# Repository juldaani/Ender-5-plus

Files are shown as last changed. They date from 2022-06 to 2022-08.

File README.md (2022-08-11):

# Ender-5-plus
Installation instructions for Ender 5 Plus (original hardware):
- BIGTREETECH BTT OCTOPUS V1.1 32BIT 
- TMC2209 stepper drivers
- Raspberry Pi 4 Model B 8GB
- OctoPi 0.18.0
- OctoPrint 1.8.1
- Klipper

### Shortcuts
[Board wirings](https://github.com/juldaani/Ender-5-plus#board-wirings)

[Installation and configuration of OctoPi+OctoPrint+Klipper](https://github.com/juldaani/Ender-5-plus#install-octopioctoprintklipper-on-raspberry-pioctopus)

[Physical installation of Octopus board and Raspberry Pi + 3D-models for mounts](https://github.com/juldaani/Ender-5-plus#physical-installation-of-octopus-board-and-raspberry-pi)

### Links
Bigtreetech octopus github:
(https://github.com/bigtreetech/BIGTREETECH-OCTOPUS-V1.0)

Random Octopus installation guide:
https://www.makenprint.uk/3d-printing/3d-printing-guides/3d-printer-mainboard-installation-guides/btt-octopus-guides/btt-octopus-setup-guide/

# Board wirings

## 1. Remove all jumpers from the board
If there are any jumpers attached remove them before proceeding.

## 2. Set jumpers to UART mode for stepper motor drivers
mtp://HMD_Global_Nokia_8_NB1GAD1780406664/Internal%20shared%20storage/DCIM/Camera/IMG_20220811_184935.jpg
mtp://HMD_Global_Nokia_8_NB1GAD1780406664/Internal%20shared%20storage/DCIM/Camera/IMG_20220811_184957.jpg

## 3. Wiring between PSU and board
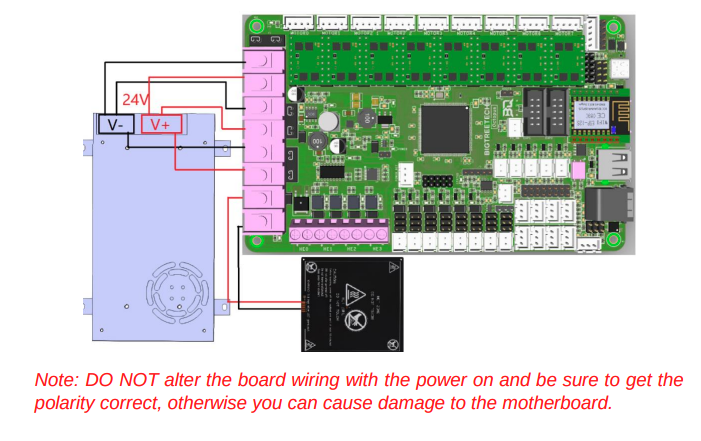
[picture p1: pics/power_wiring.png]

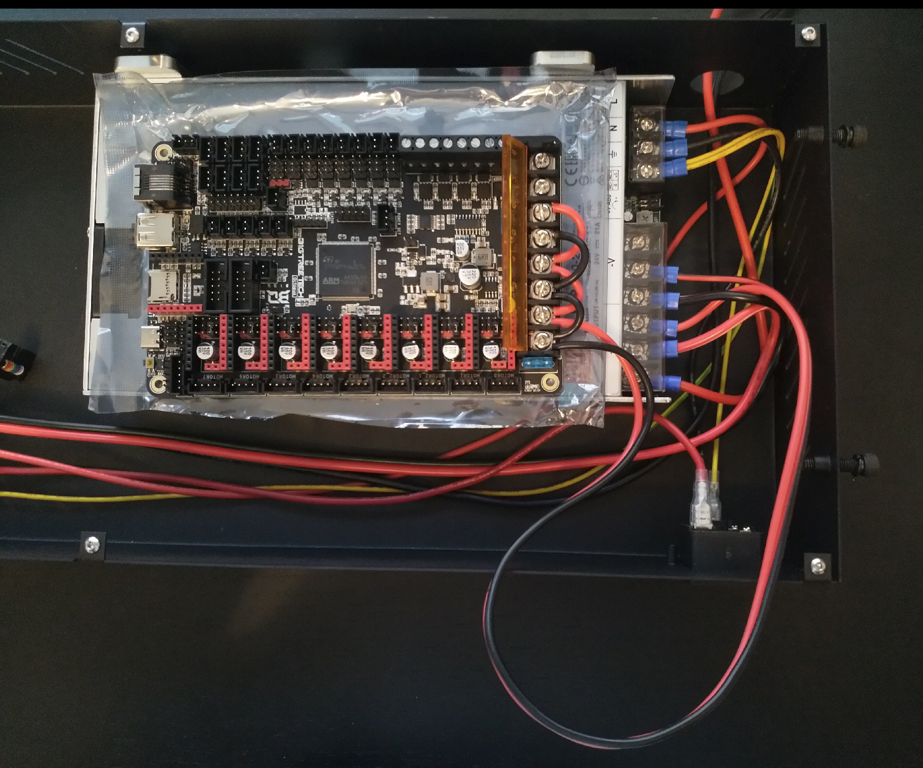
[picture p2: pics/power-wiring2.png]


## 4. Hot bed wiring
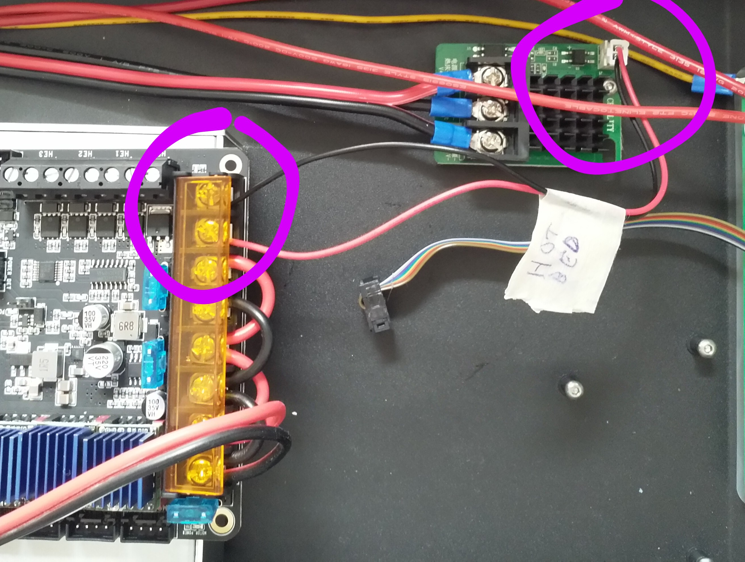
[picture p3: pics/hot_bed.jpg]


## 5. Install TMC2209 stepper motor drivers
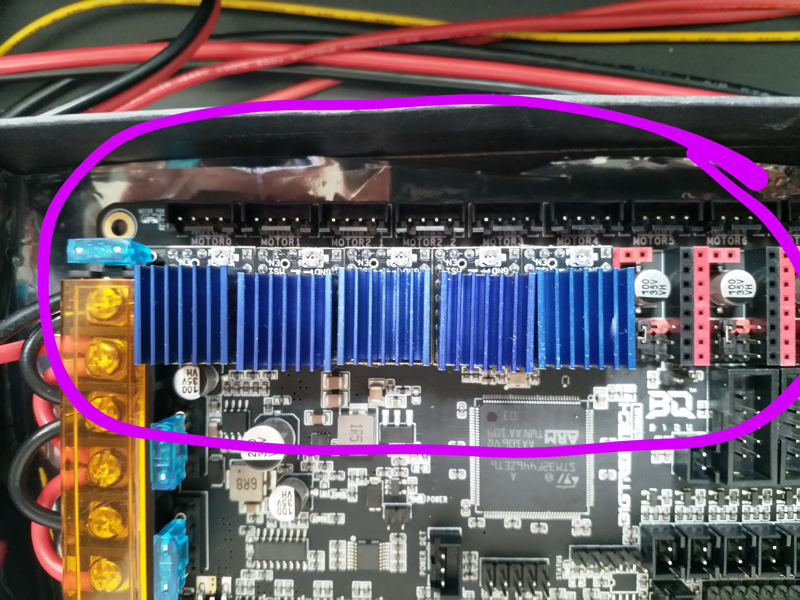
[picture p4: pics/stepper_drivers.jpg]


## 7. Plug in stepper motor cables
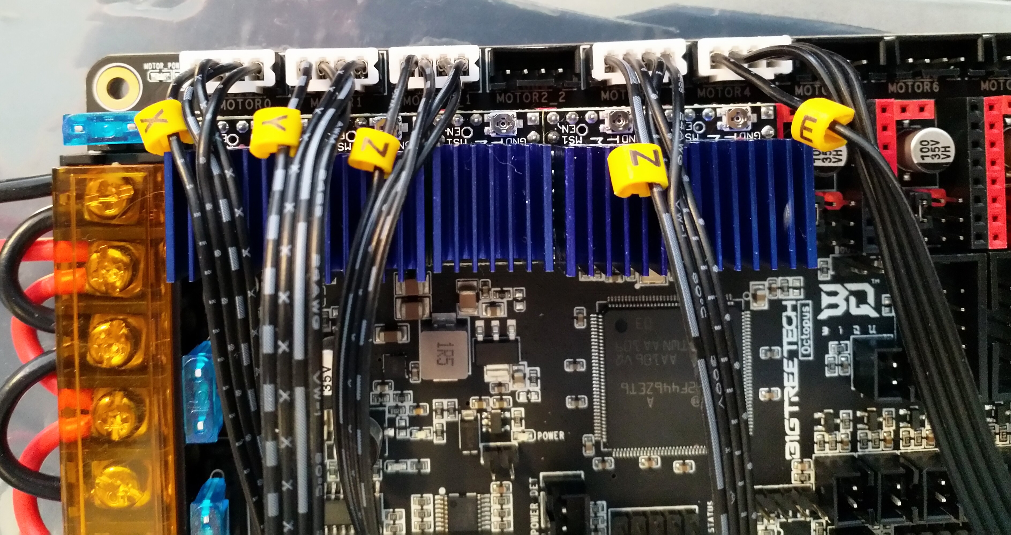
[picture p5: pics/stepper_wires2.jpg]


- MOTOR0: X
- MOTOR1: Y
- MOTOR2_1: Z
- MOTOR3: Z
- MOTOR4: EXTRUDER (E)

## 8. Change X and Y-axis limit switch connectors to 3-pin
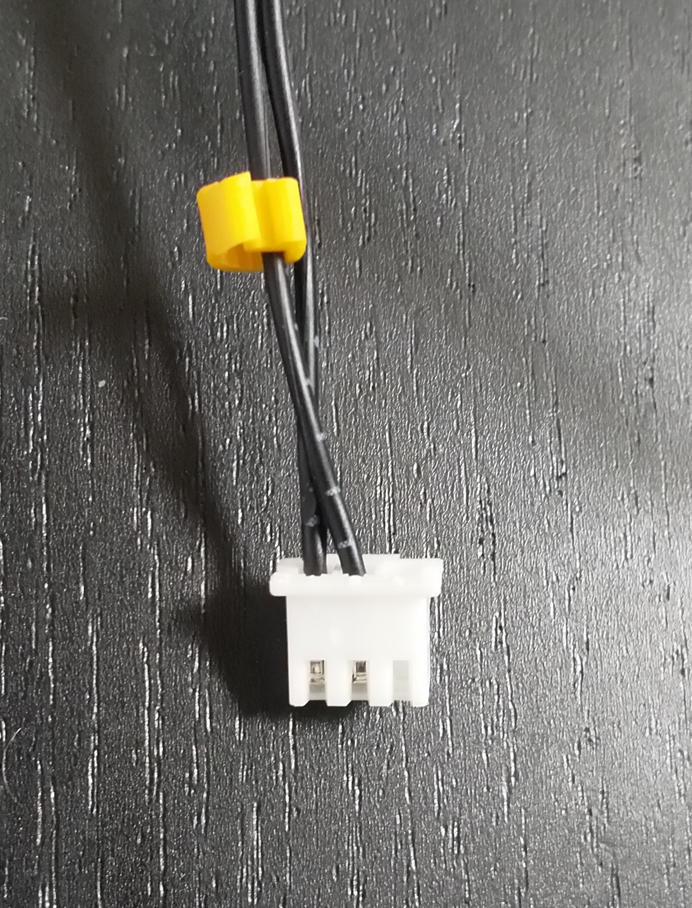
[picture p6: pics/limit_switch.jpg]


## 9. Plug Y-axis limit switch connector to DIAG1
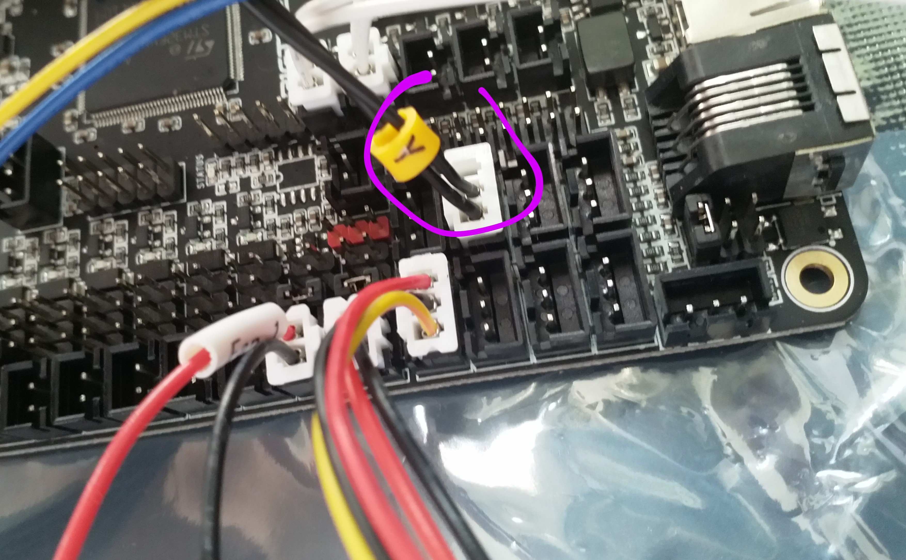
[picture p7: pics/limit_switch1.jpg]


## 10. Plug X-axis limit switch connector to DIAG0
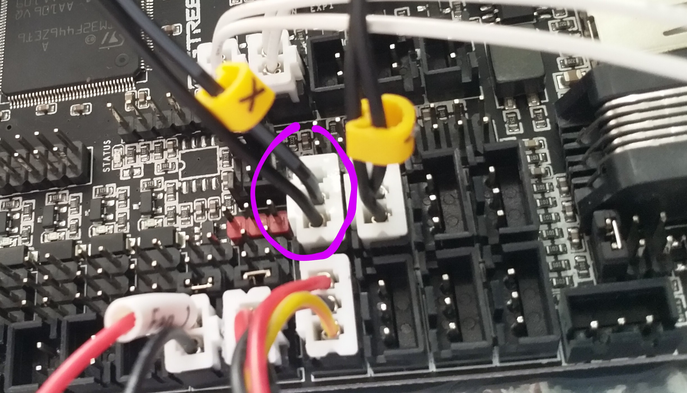
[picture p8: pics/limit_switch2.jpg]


## 11. Connect Nozzle Heat to HE0
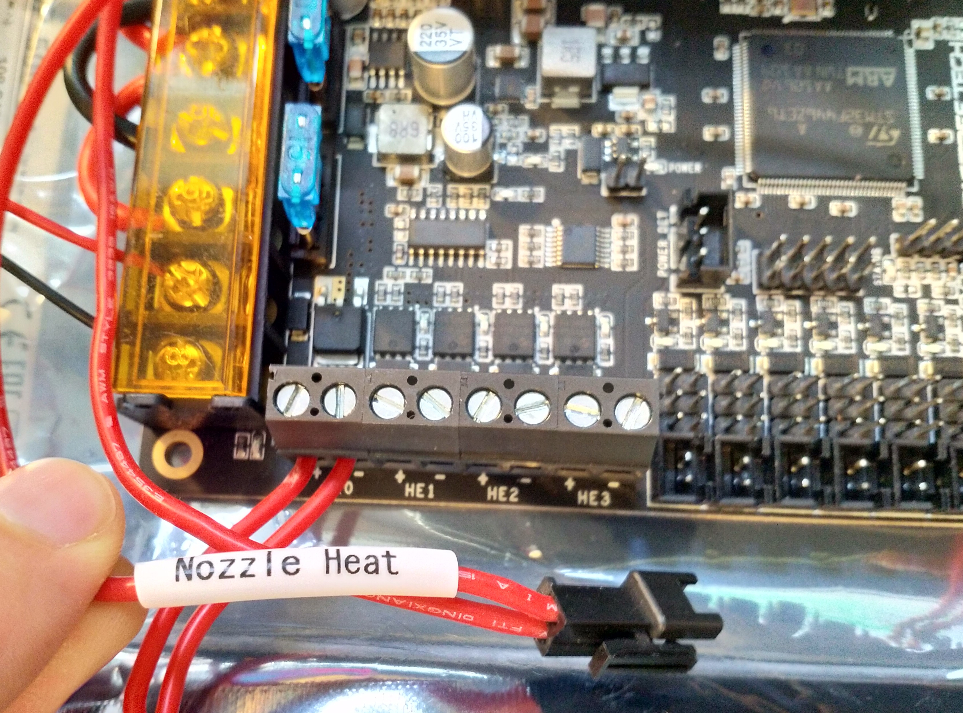
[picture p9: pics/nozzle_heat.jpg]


## 12. Connect Bed Thermistor to TB
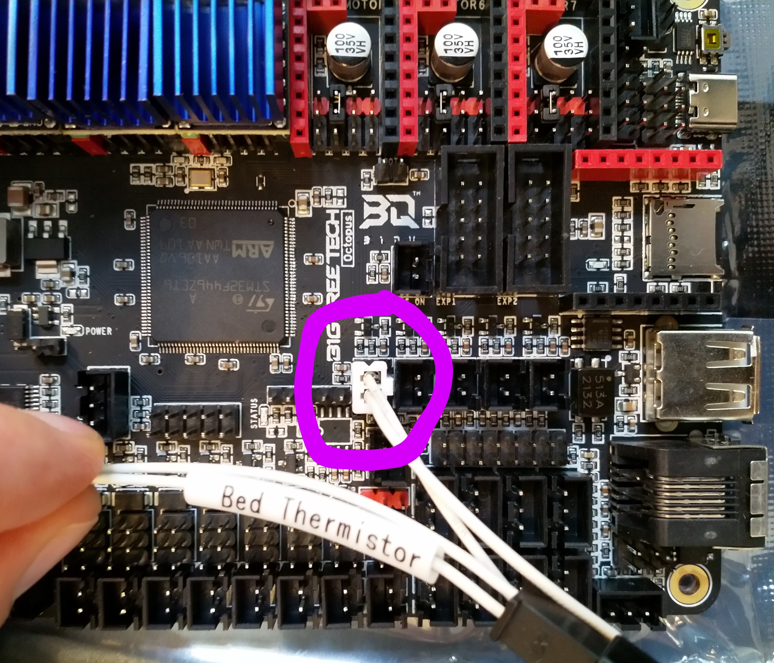
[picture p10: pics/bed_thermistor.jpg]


## 13. Connect Nozzle Thermistor to T0
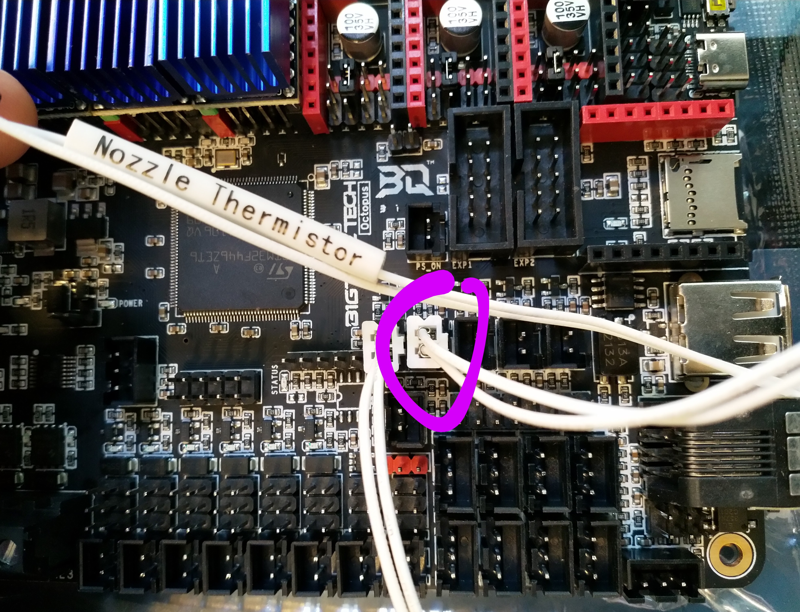
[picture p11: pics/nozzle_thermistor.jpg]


## 14. Connect BlTouch
Change original connector to Dupont connector:

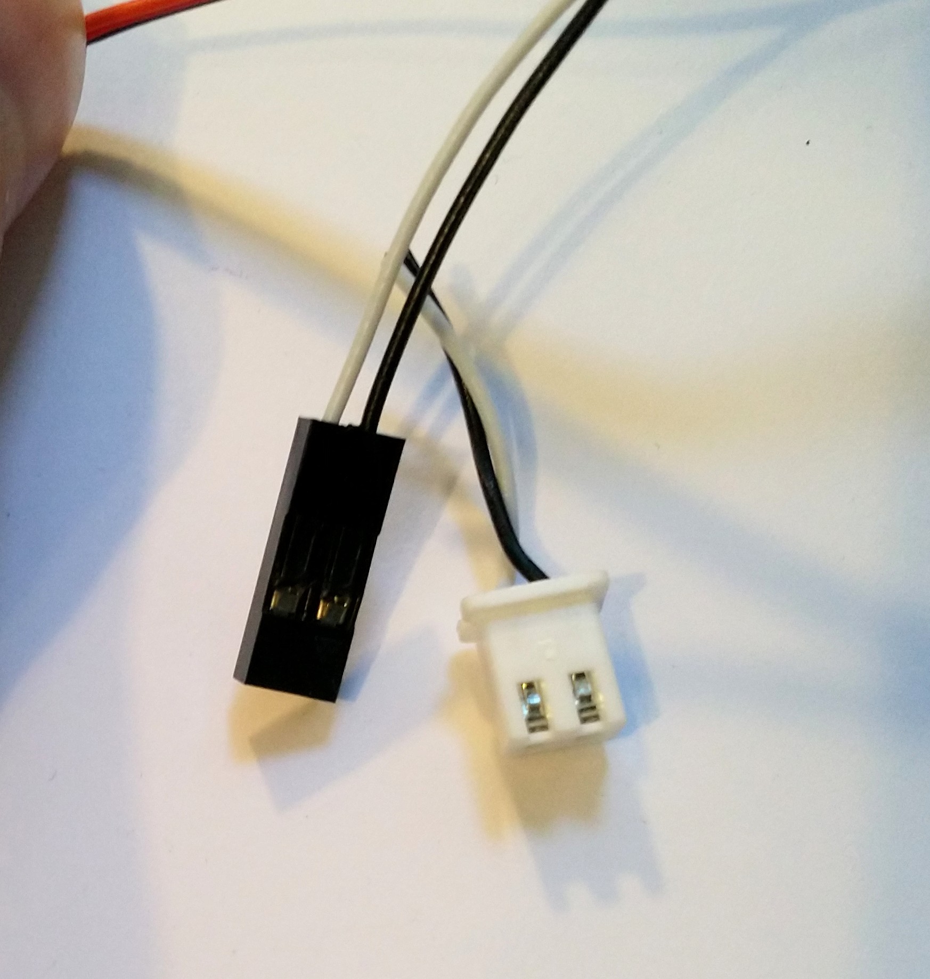
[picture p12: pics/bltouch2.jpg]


Swap wires in connectors according to the image and plug connectors to BlTouch pins:

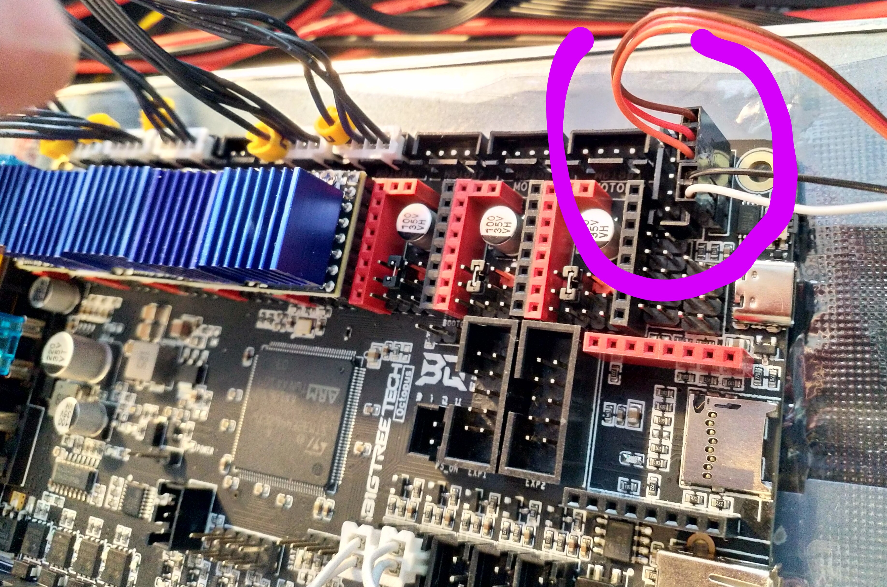
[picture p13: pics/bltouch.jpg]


## 15. Connect filament runout sensor to DIAG4
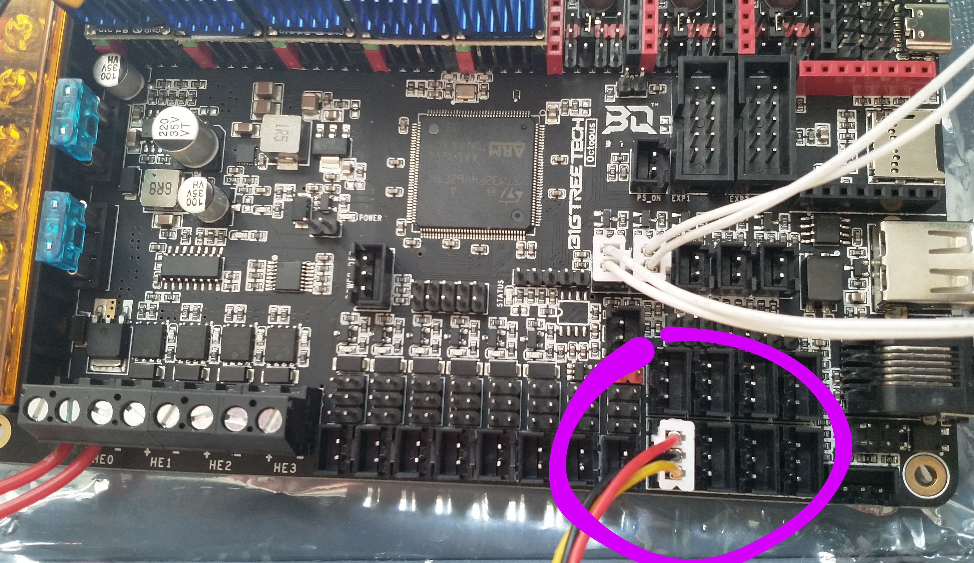
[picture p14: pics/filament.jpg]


## 16. Set fan jumpers
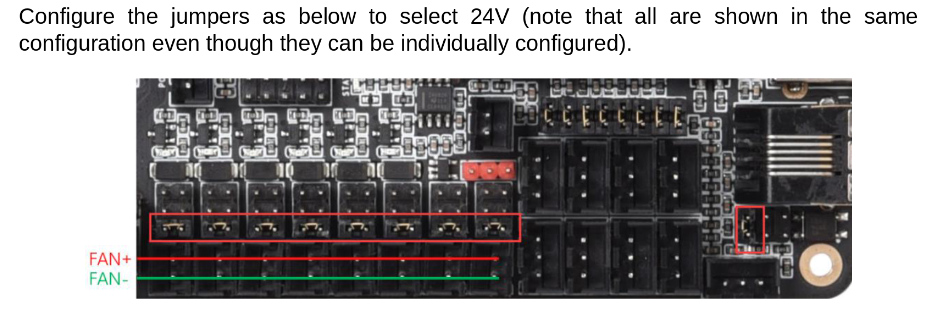
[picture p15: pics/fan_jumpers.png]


## 17. Plug part cooling fan to FAN0 (PWM)
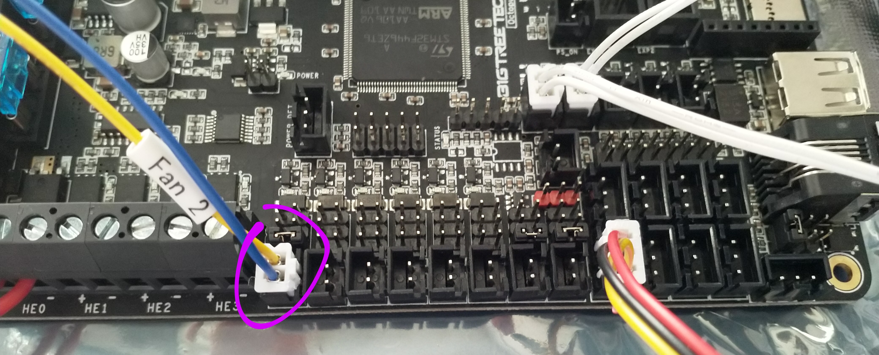
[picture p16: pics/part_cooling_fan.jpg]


## 18. Plug mainboard fan to FAN7 (always on)
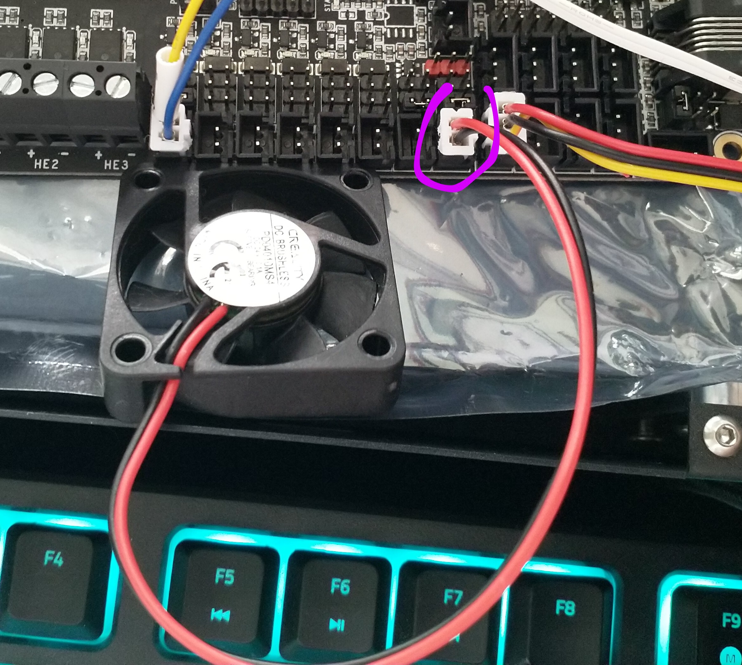
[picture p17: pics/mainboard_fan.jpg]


## 19. Plug extruder fan to FAN6 (always on)
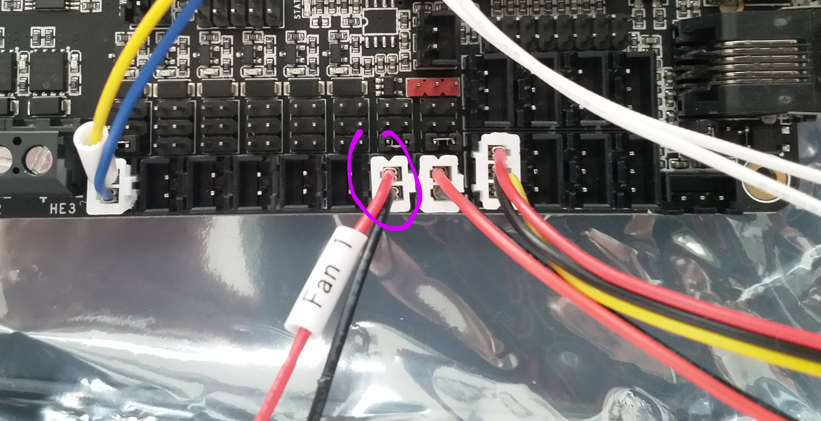
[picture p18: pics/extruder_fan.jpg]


## 20. Connect Raspberry to Octopus board
- Connect Raspberry and Octopus via USB-C
- Power Raspberry through GPIO pins
- Raspberry pins 2,4 (5V) -> Octopus Raspberry (J26 connector) 5V pins
- Raspberry pins 6,9 (GND) -> Octopus Raspberry (J26 connector) GND pins
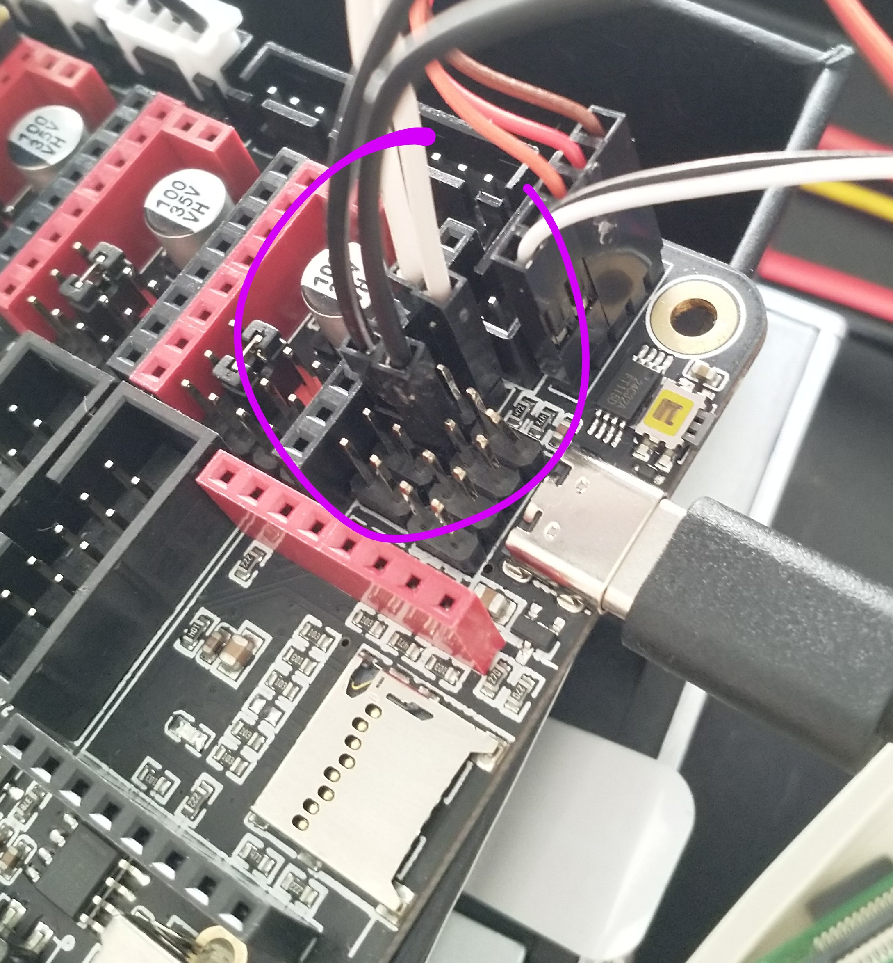
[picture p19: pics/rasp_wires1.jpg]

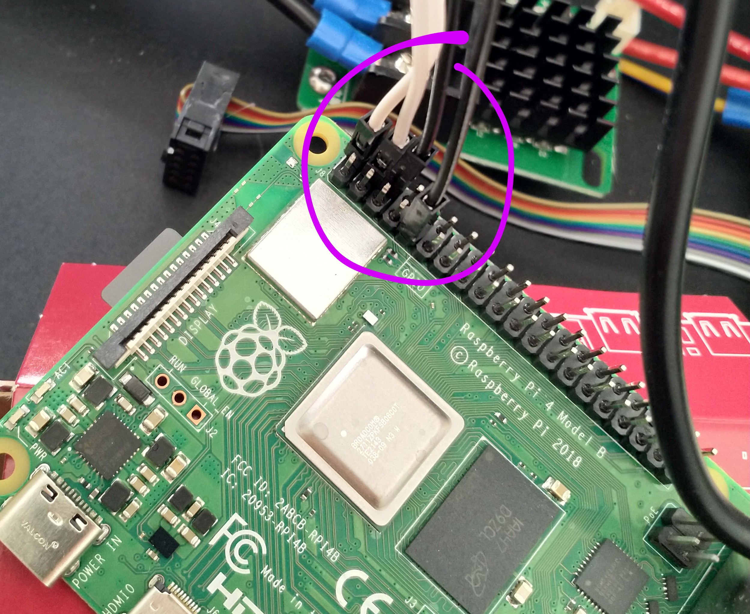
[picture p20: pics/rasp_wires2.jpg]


# Install OctoPi+OctoPrint+Klipper on Raspberry Pi+Octopus

## 1. Download Raspberry Pi Imager
https://www.raspberrypi.com/software/

## 2. Install OctoPi using Raspberry Pi Imager
- CHOOSE OS -> Other specific-purpose OS -> 3D printing -> OctoPi
- Hit CTRL+SHIFT+X to access advanced options
- Enable SSH and set username and password
- Configure wireless LAN (SSID, Password, Wireless LAN country)
- Set locale settings (Time zone, Keyboard layout)

## 3. Check OctoPi is working
- Plug in power input cable into Raspberry USB-C slot
- Put SD card in
- Type "http://octopi.local" to browser
- If everything works as expected OctoPrint web page should be opened

## 4. Install Klipper
https://www.klipper3d.org/Installation.html#prepping-an-os-image
1. Check that connections and wires are ok (no short circuits etc.)
2. Switch power supply on. Beware that the input voltage to the PSU might be fatal so don't put your fingers to wrong places.  
3. Connect to Raspberry via SSH. Linux command: ```ssh pi@octopi.local```
4. ```git clone https://github.com/Klipper3d/klipper```
5. ```./klipper/scripts/install-octopi.sh```

## 5. Build and flash Octopus board
https://www.klipper3d.org/Installation.html#building-and-flashing-the-micro-controller

https://github.com/bigtreetech/BIGTREETECH-OCTOPUS-V1.0/tree/master/Firmware/Klipper#build-firmware-image

https://github.com/bigtreetech/BIGTREETECH-OCTOPUS-V1.0/tree/master/Firmware/Klipper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

[https://docs.vorondesign.com/build/software/octopus_klipper.html](https://docs.vorondesign.com/build/software/octopus_klipper.html#option-2-dfu-firmware-install)
1. SSH into raspberry. Linux command: ```ssh pi@octopi.local```
2. ```cd ~/klipper/```
3. ```export LC_ALL=en_GB.UTF-8```
4. ```make menuconfig```
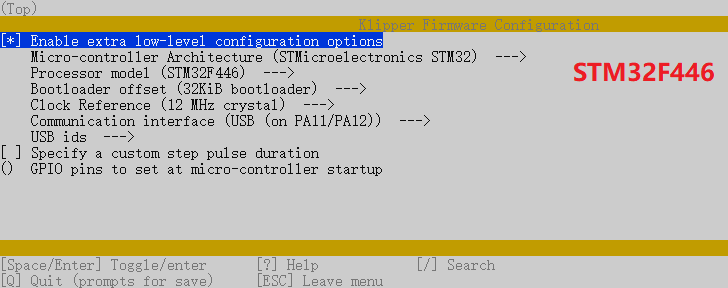
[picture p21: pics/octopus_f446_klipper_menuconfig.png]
5. Set following configurations: 
6. ```make```
7. Power everything off
8. Install jumper to BOOT0 on Octopus board
9. Power on
10. SSH into Raspberry
11. ```cd ~/klipper/```
12. <i>"When flashing for the first time, make sure that OctoPrint is not connected directly to the printer (from the OctoPrint web page, under the "Connection" section, click "Disconnect")."</i>
13. <i>"From your ssh session, run ```lsusb```. and find the ID of the dfu device. The device is typically named STM Device in DFU mode."</i>
14. <i>"If you do not see a DFU device in the list, press the reset button next to the USB connector and run lsusb again."</i>
15. <i>"Run ```make flash FLASH_DEVICE=1234:5678``` replace 1234:5678 with the ID from the previous step"</i>
16. Power everything off
17. Remove jumper from BOOT0
18. Power on
19. SSH into Raspberry
20. <i>"You can confirm that the flash was successful, by running ```ls /dev/serial/by-id```. If the flash was successful, this should now show a klipper device, similar to: <br> "</i>

## 6. Configure OctoPrint to use Klipper
https://www.klipper3d.org/Installation.html#configuring-octoprint-to-use-klipper

## 7. Configure Klipper
https://www.klipper3d.org/Installation.html#configuring-klipper

1. SSH into Raspberry
2. ```cp ~/klipper/config/generic-bigtreetech-octopus.cfg ~/printer.cfg```
3. Run ```ls /dev/serial/by-id/*``` command in Raspberry to get the ID number of the Octopus board.
4. Run ```nano ~/printer.cfg``` and set the ID number under ```[mcu]``` section in printer.cfg: <br> ```serial: /dev/serial/by-id/usb-Klipper_stm32f446xx_0E002B00135053424E363620-if00```
5. Power everything off
7. Connect wires to the printer
8. Power on
9. Open http://octopi.local and connect to the printer
10. Open Terminal tab, type ```status``` and hit Send button.
11. If everything is ok a "status" command will report the printer is ready if the Klipper config file is successfully read and the micro-controller is successfully found and configured: <br> 

## 8. (Optional) Install sshfs
Install sshfs (for mounting Raspberry's file system over SSH) to avoid serious mental health issues with nano text editor when customizing printer.cfg.

1. Install sshfs, Linux command: ```sudo apt install sshfs```
2. ```sudo mkdir /mnt/ender```
3. Mount Raspberry's filesystem: ```sudo sshfs -o allow_other,default_permissions pi@octopi.local:/ /mnt/ender```
4. Open printer configuration file with gedit: ```gedit /mnt/ender/home/pi/printer.cfg```
5. Set gedit Highlight Mode to YAML to make the text more readable

## 9. Upload printer.cfg to raspberry
https://www.klipper3d.org/Installation.html#configuring-klipper

1. Configuration file: https://github.com/juldaani/Ender-5-plus/blob/main/printer-original-hardware.cfg
2. Rename to "printer.cfg" before using with Klipper
3. Update [mcu] section (https://github.com/juldaani/Ender-5-plus/blob/main/README.md#7-configure-klipper)

<i>"After creating and editing the file it will be necessary to issue a "restart" command in the OctoPrint web terminal to load the config. A "status" command will report the printer is ready if the Klipper config file is successfully read and the micro-controller is successfully found and configured.

When customizing the printer.cfg file, it is not uncommon for Klipper to report a configuration error. If an error occurs, make any necessary corrections to the printer config file and issue "restart" until "status" reports the printer is ready."</i>

## 10. Configuration checks
https://www.klipper3d.org/Config_checks.html

https://www.klipper3d.org/BLTouch.html#initial-tests

## 11. Calibrations and adjustments
### BLTouch and nozzle offsets
[https://www.klipper3d.org/Probe_Calibrate.html](https://www.klipper3d.org/Probe_Calibrate.html)

<i>"During calibration it may be necessary to set the printer's Z position_min to a negative number (eg, position_min = -2). The printer enforces boundary checks even during calibration routines. Setting a negative number allows the printer to move below the nominal position of the bed, which may help when trying to determine the actual bed position."</i> <b>(change this in printer.cfg under [stepper_z] section)</b>

### Bed tilt using bed levelling screws
https://www.klipper3d.org/Manual_Level.html#adjusting-bed-leveling-screws-using-the-bed-probe

### Bed mesh
https://www.klipper3d.org/Bed_Mesh.html

### Extruder rotation distance
https://www.klipper3d.org/Rotation_Distance.html#calibrating-rotation_distance-on-extruders

# Physical installation of Octopus board and Raspberry Pi
FreeCAD and stl models for mounts for Raspberry Pi and Octopus: https://github.com/juldaani/Ender-5-plus/tree/main/3d-models

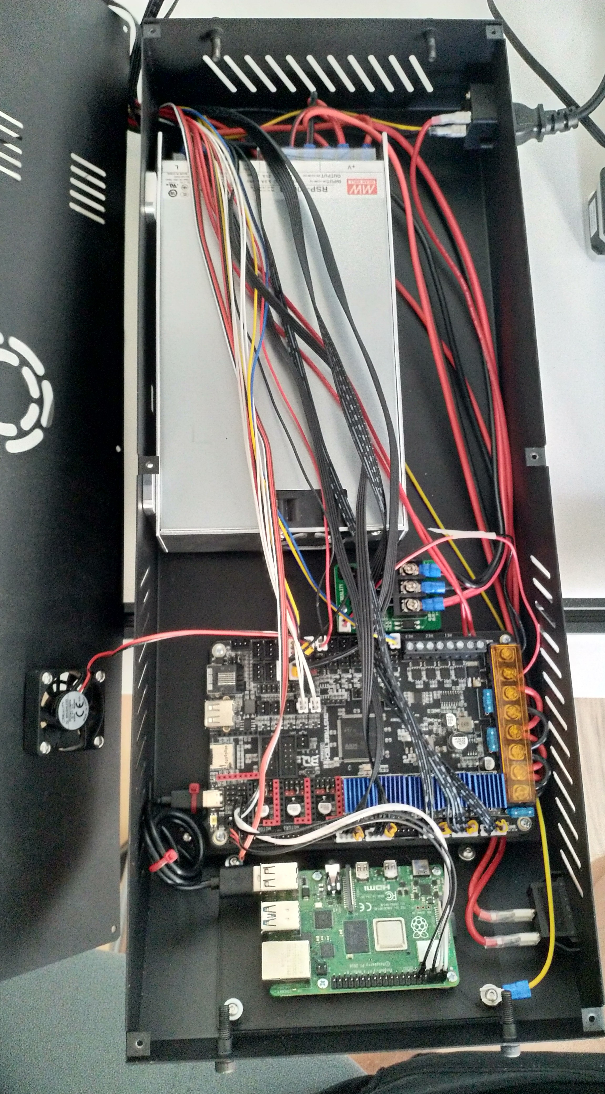
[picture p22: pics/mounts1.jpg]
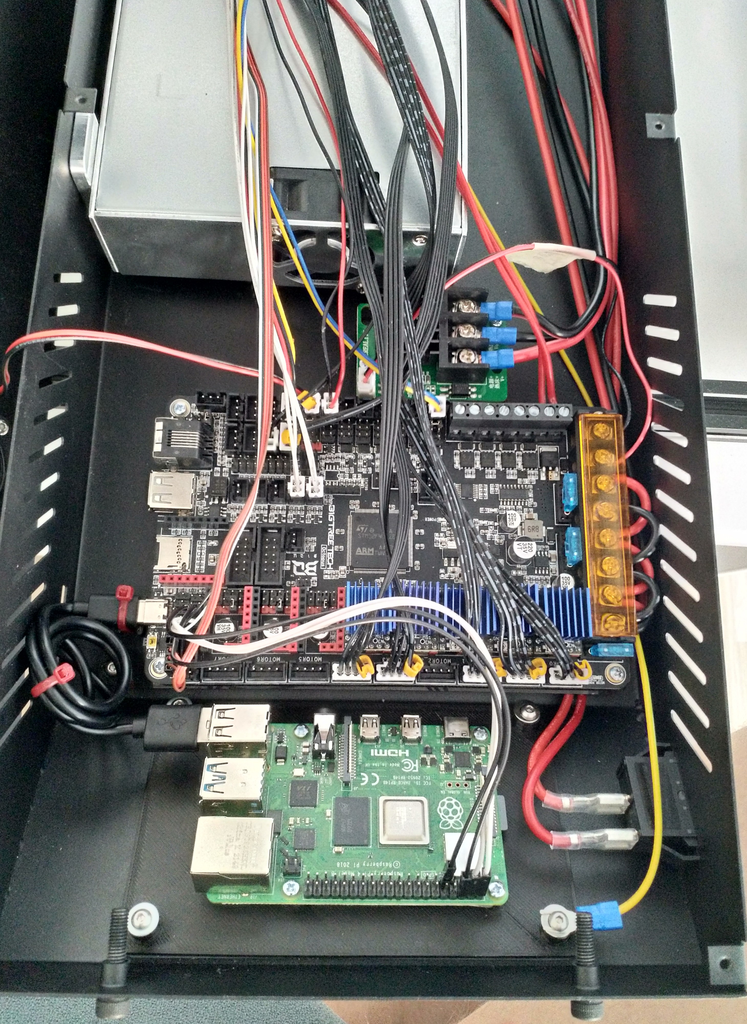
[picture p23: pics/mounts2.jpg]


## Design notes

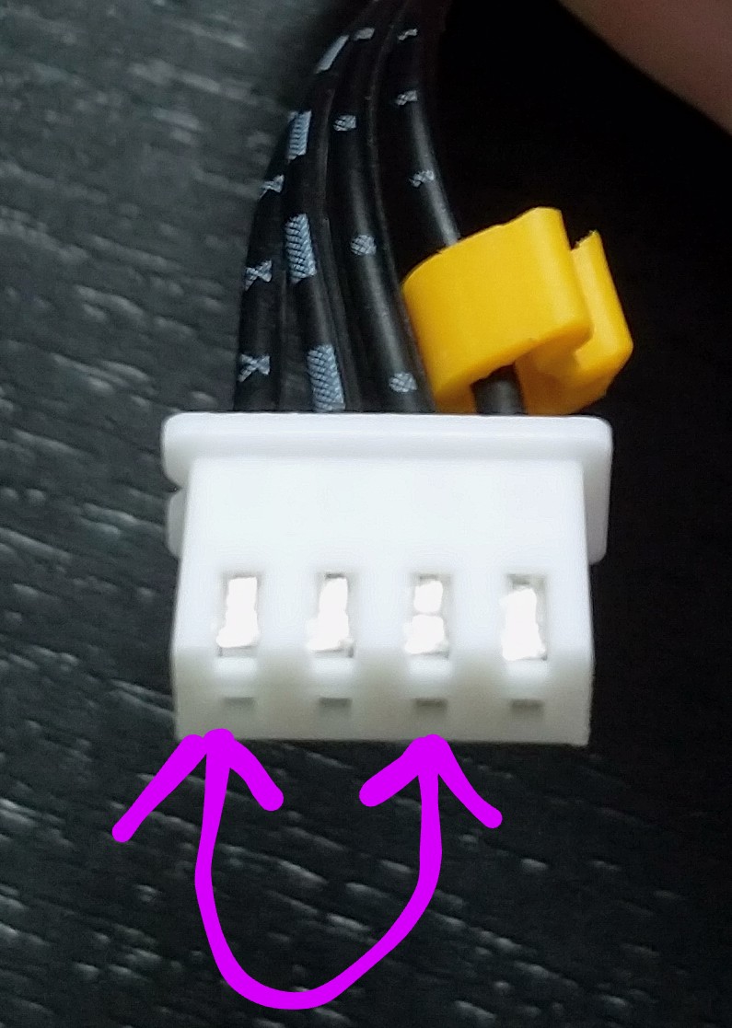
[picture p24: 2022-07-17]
pics/stepper_wires.jpg

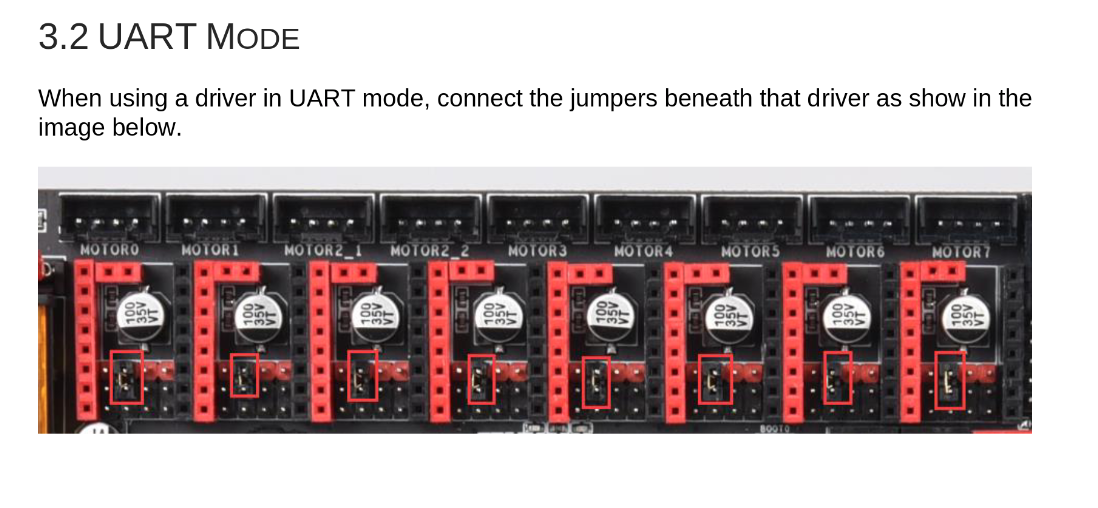
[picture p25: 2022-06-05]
pics/uart-jumpers.png

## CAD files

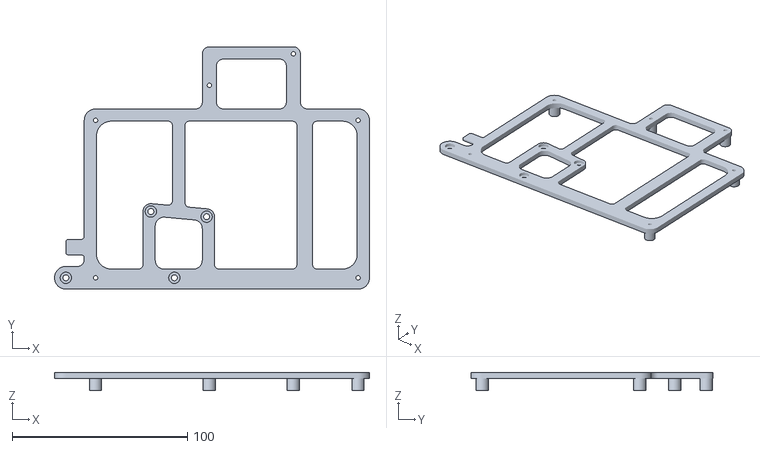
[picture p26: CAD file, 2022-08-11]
3d-models/octopus_adapter.stl
180.0 x 138.5 x 10.5

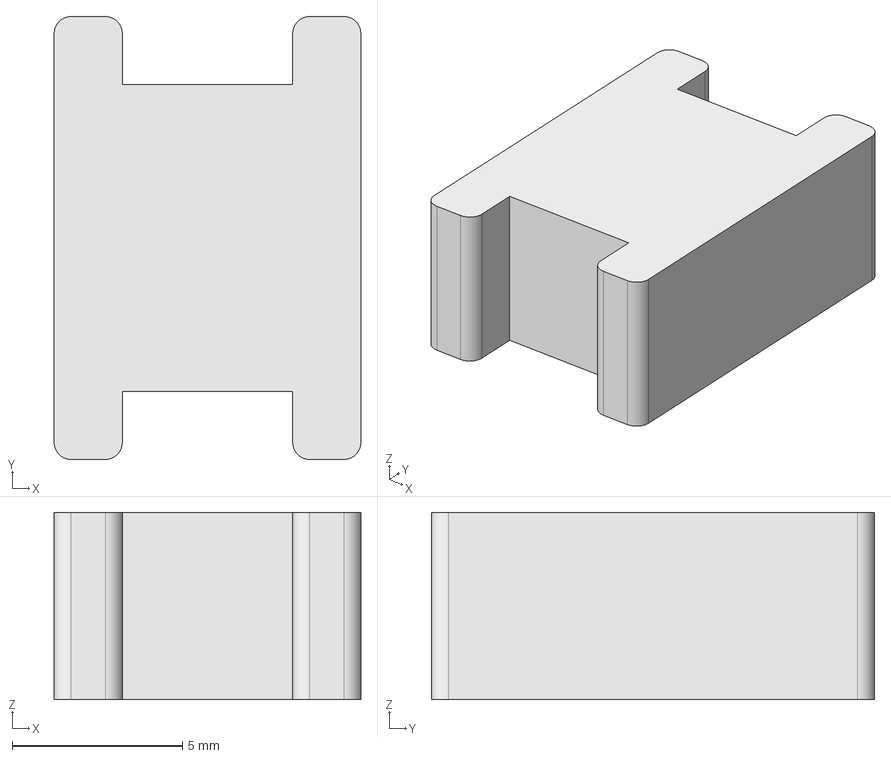
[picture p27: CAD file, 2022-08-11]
3d-models/usb_cable_support.FCStd
9.00 x 13.0 x 5.50 mm

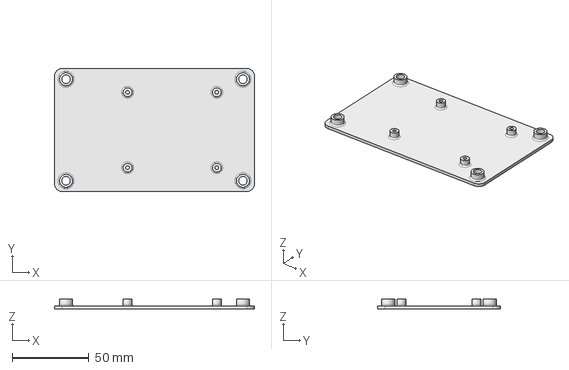
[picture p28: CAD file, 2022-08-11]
3d-models/rasp_mount.FCStd
130.0 x 80.0 x 6.50 mm

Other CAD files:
3d-models/rasp_mount.stl
3d-models/usb_cable_support.stl

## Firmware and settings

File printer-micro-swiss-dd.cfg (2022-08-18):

# This file contains common pin mappings for the BigTreeTech Octopus.
# To use this config, the firmware should be compiled for the
# STM32F446 with a "32KiB bootloader" and a "12MHz crystal" clock reference.

[mcu]
serial: /dev/serial/by-id/usb-Klipper_stm32f446xx_3B0052000851303432383339-if00
# CAN bus is also available on this board

[temperature_sensor mcu_temp]
sensor_type: temperature_mcu

[printer]
kinematics: cartesian
max_velocity: 300
max_accel: 4500
max_z_velocity: 10
max_z_accel: 100

[board_pins] 	# EXP1 / EXP2 (display) pins
aliases:
    # EXP1 header
    EXP1_1=PE8, EXP1_2=PE7,
    EXP1_3=PE9, EXP1_4=PE10,
    EXP1_5=PE12, EXP1_6=PE13,    # Slot in the socket on this side
    EXP1_7=PE14, EXP1_8=PE15,
    EXP1_9=<GND>, EXP1_10=<5V>,

    # EXP2 header
    EXP2_1=PA6, EXP2_2=PA5,
    EXP2_3=PB1, EXP2_4=PA4,
    EXP2_5=PB2, EXP2_6=PA7,      # Slot in the socket on this side
    EXP2_7=PC15, EXP2_8=<RST>,
    EXP2_9=<GND>, EXP2_10=<5V>

[stepper_x]
step_pin: PF13
dir_pin: !PF12
enable_pin: !PF14
microsteps: 256
rotation_distance: 40
endstop_pin: ^PG6
position_endstop: 350
position_max: 350
homing_speed: 100

[tmc2209 stepper_x]
uart_pin: PC4
#diag_pin: PG6
run_current: 0.7
interpolate: False
#stealthchop_threshold: 999999

[stepper_y]
step_pin: PG0
dir_pin: !PG1
enable_pin: !PF15
microsteps: 256
rotation_distance: 40
endstop_pin: ^PG9
position_endstop: 350
position_max: 350
homing_speed: 100

[tmc2209 stepper_y]
uart_pin: PD11
#diag_pin: PG9
run_current: 0.7
interpolate: False
#stealthchop_threshold: 999999

[stepper_z]
step_pin: PF11
dir_pin: !PG3
enable_pin: !PG5
microsteps: 256
rotation_distance: 4
endstop_pin: probe:z_virtual_endstop
position_max: 400
position_min: 0.0
homing_speed: 10.0

[tmc2209 stepper_z]
uart_pin: PC6
#diag_pin: PG10
run_current: 0.650
interpolate: False
#stealthchop_threshold: 999999

[stepper_z1]
step_pin: PG4
dir_pin: !PC1
enable_pin: !PA0
microsteps: 256
rotation_distance: 4
#endstop_pin: probe:z_virtual_endstop
#position_max: 400
#position_min: 0
#homing_speed: 10.0

[tmc2209 stepper_z1]
uart_pin: PC7
#diag_pin: PG11
run_current: 0.650
interpolate: False
#stealthchop_threshold: 999999

[extruder]
step_pin: PF9
dir_pin: !PF10
enable_pin: !PG2
microsteps: 256
rotation_distance: 23.160
nozzle_diameter: 0.400
filament_diameter: 1.750
heater_pin: PA2 # HE0
sensor_pin: PF4 # T0
sensor_type: EPCOS 100K B57560G104F
control: pid
pid_Kp: 22.2
pid_Ki: 1.08
pid_Kd: 114
min_temp: 0
max_temp: 320

[tmc2209 extruder]
uart_pin: PF2
run_current: 0.700
interpolate: False
#stealthchop_threshold: 999999

#[tmc2209 extruder1]
#uart_pin: PE4
#run_current: 0.800
#stealthchop_threshold: 999999

#[tmc2209 extruder2]
#uart_pin: PE1
#run_current: 0.800
#stealthchop_threshold: 999999

#[tmc2209 extruder3]
#uart_pin: PD3
#run_current: 0.800
#stealthchop_threshold: 999999

[filament_switch_sensor filament_sensor]
switch_pin: PG12

[bltouch]
sensor_pin: ^PB7
control_pin: PB6
x_offset: -43.0
y_offset: -7.0
#z_offset: 0
speed: 3.0
pin_up_touch_mode_reports_triggered: False

[safe_z_home]
home_xy_position: 200, 175
speed: 150
z_hop: 10
z_hop_speed: 10

[heater_bed]
heater_pin: PA1
sensor_pin: PF3 # TB
sensor_type: EPCOS 100K B57560G104F
control: pid
pid_Kp: 690.34
pid_Ki: 111.47
pid_Kd: 1068.83
min_temp: 0
max_temp: 130

[fan]	# Part cooling fan
pin: PA8  # FAN0

#[heater_fan fan1]
#pin: PE5

#[heater_fan fan2]
#pin: PD12

#[heater_fan fan3]
#pin: PD13

#[heater_fan fan4]
#pin: PD14

#[controller_fan fan5]
#pin: PD15

[screws_tilt_adjust]
screw1: 55, 35
screw1_name: front left screw
screw2: 345, 35
screw2_name: front right screw
screw3: 345, 305
screw3_name: rear right screw
screw4: 55, 305
screw4_name: rear left screw
horizontal_move_z: 5.
speed: 300
screw_thread: CW-M4

[bed_mesh]
speed: 300
horizontal_move_z: 4.5
mesh_min: 15, 15
mesh_max: 305, 305
mesh_pps: 3, 3
probe_count: 5, 5

[z_tilt]
z_positions:
    370, 165
    -40, 165
points:
    55, 35
    345, 35
    345, 305
    55, 305
speed: 300
horizontal_move_z: 7.5

#*# <---------------------- SAVE_CONFIG ---------------------->
#*# DO NOT EDIT THIS BLOCK OR BELOW. The contents are auto-generated.
#*#
#*# [bltouch]
#*# z_offset = 2.170
#*#
#*# [bed_mesh default]
#*# version = 1
#*# points =
#*# 	  -0.186484, -0.132422, -0.127188, -0.123438, -0.159688
#*# 	  -0.108984, -0.051094, -0.030703, -0.027500, -0.073672
#*# 	  -0.069297, -0.012969, 0.020625, 0.010703, -0.053281
#*# 	  -0.087578, -0.044453, -0.030781, -0.024375, -0.088438
#*# 	  -0.231406, -0.228203, -0.232188, -0.232656, -0.253516
#*# tension = 0.2
#*# min_x = 15.0
#*# algo = lagrange
#*# y_count = 5
#*# mesh_y_pps = 3
#*# min_y = 15.0
#*# x_count = 5
#*# max_y = 305.0
#*# mesh_x_pps = 3
#*# max_x = 305.0
